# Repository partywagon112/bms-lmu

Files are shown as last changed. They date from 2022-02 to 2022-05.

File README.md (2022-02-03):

# Battery Management System - Local Measurement Unit

Final Year Research Project (FYRP) by Ethan Suter and Patrick Curtain to design a battery management system for an electric solar vehicle.

The Local Measurement Unit (LMU) is used to relay information about the cells to the Central Management Unit (CMU) that will they respond with balance target values for the LMU to act on. The LMU interconnects to the cell stack with the use of a terminal board, contained within the same repository. 

The LMU features an LTC6811 to monitor the cells, with two LTC3300 to actively balance the stack. These connect through multiple isolated SPI interfaces, to a microcontroller that is used to preprocess the data into a simpler form for the CMU to decypher.

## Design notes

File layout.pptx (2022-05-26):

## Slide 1

TEMP

TEMPERATURE

1

3

LV

OUT

10

IN

8

ABAL_1

5

PBAL

9

11

2

4

6

7

ABAL_2

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
RULES:
- The Active balancer, Passive balancer and temperature modules should be placed in proximity to the LV zone for SPI to cross isolation line
- 6 Must be adjacent to 7
- The balancer must be placed equidistance from each module in it’s balance group.
- The Temperature module should be placed on the ground that covers PBAL and ABAL (GND_LOWER)
- Along the vertical axis, each module should be in sequential order.

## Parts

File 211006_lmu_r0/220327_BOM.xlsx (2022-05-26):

Item | Qty | Reference(s) | Value | LibPart | Footprint | Datasheet | AVAILABILITY | Description | Height | MANUFACTURER | MAXIMUM_PACKAGE_HEIGHT | MP | Manufacturer | Mouser Part Number | Mouser Price/Stock | Mouser URL | PACKAGE | PARTREV | PRICE | Part Number | SNAPEDA_PACKAGE_ID | STANDARD | Voltage
1 | 1 | C1 | 220uF | Device:C_Polarized_US | Capacitor_SMD:CP_Elec_10x12.5 | ~ |  |  |  |  |  |  | Vishay | 594-MAL214699106E3 |  | https://au.mouser.com/ProductDetail/Vishay-BC-Components/MAL214699106E3 |  |  |  | MAL214699106E3
2 | 2 | C2, C3 | 10uF | Device:C | Capacitor_SMD:C_0805_2012Metric_Pad1.18x1.45mm_HandSolder | ~ |  |  |  |  |  |  |  |  |  |  |  |  |  | -
3 | 2 | C4, C6 | 22uF | Device:C | Capacitor_SMD:C_0805_2012Metric_Pad1.18x1.45mm_HandSolder | ~ |  |  |  |  |  |  |  |  |  |  |  |  |  | -
4 | 17 | C5, C12, C13, C25, C26, C27, C30, C103, C176, C177, C178, C179, C180, C181, C184, C185, C186 | 100nF | Device:C | Capacitor_SMD:C_0603_1608Metric_Pad1.08x0.95mm_HandSolder | ~ |  |  |  |  |  |  |  |  |  |  |  |  |  | -
5 | 22 | C7, C17, C18, C19, C20, C21, C22, C23, C24, C41, C53, C65, C77, C89, C101, C114, C126, C138, C150, C162, C174, C182 | 10nF | Device:C | Capacitor_SMD:C_0603_1608Metric_Pad1.08x0.95mm_HandSolder | ~ |  |  |  |  |  |  |  |  |  |  |  |  |  | -
6 | 4 | C8, C9, C10, C11 | DNP 10pF | Device:C | Capacitor_SMD:C_0603_1608Metric_Pad1.08x0.95mm_HandSolder | ~ |  |  |  |  |  |  |  |  |  |  |  |  |  | -
7 | 3 | C14, C15, C16 | 1uF | Device:C | Capacitor_SMD:C_0603_1608Metric_Pad1.08x0.95mm_HandSolder | ~ |  |  |  |  |  |  |  |  |  |  |  |  |  | -
8 | 2 | C28, C29 | 100nF | Device:C | Capacitor_SMD:C_0805_2012Metric_Pad1.18x1.45mm_HandSolder | ~ |  |  |  |  |  |  |  |  |  |  |  |  |  | -
9 | 72 | C31, C32, C34, C37, C39, C40, C43, C44, C46, C49, C51, C52, C55, C56, C58, C61, C63, C64, C67, C68, C70, C73, C75, C76, C79, C80, C82, C85, C87, C88, C91, C92, C94, C97, C99, C100, C104, C105, C107, C110, C112, C113, C116, C117, C119, C122, C124, C125, C128, C129, C131, C134, C136, C137, C140, C141, C143, C146, C148, C149, C152, C153, C155, C158, C160, C161, C164, C165, C167, C170, C172, C173 | 100uF | Device:C | Capacitor_SMD:C_1206_3216Metric_Pad1.33x1.80mm_HandSolder | ~ |  |  |  |  |  |  |  |  |  |  |  |  |  |  |  |  | 100V
10 | 12 | C33, C45, C57, C69, C81, C93, C106, C118, C130, C142, C154, C166 | 2.2nF | Device:C | Capacitor_SMD:C_0603_1608Metric_Pad1.08x0.95mm_HandSolder | ~ |  |  |  |  |  |  |  |  |  |  |  |  |  | -
11 | 36 | C35, C36, C38, C47, C48, C50, C59, C60, C62, C71, C72, C74, C83, C84, C86, C95, C96, C98, C108, C109, C111, C120, C121, C123, C132, C133, C135, C144, C145, C147, C156, C157, C159, C168, C169, C171 | 470pF | Device:C | Capacitor_SMD:C_0603_1608Metric_Pad1.08x0.95mm_HandSolder | ~ |  |  |  |  |  |  |  |  |  |  |  |  |  |  |  |  | 100V
12 | 12 | C42, C54, C66, C78, C90, C102, C115, C127, C139, C151, C163, C175 | DNP 10nF | Device:C | Capacitor_SMD:C_0805_2012Metric_Pad1.18x1.45mm_HandSolder | ~ |  |  |  |  |  |  |  |  |  |  |  |  |  |  |  |  | 100V
13 | 1 | C183 | 1uF | Device:C | Capacitor_SMD:C_0805_2012Metric_Pad1.18x1.45mm_HandSolder | ~ |  |  |  |  |  |  |  |  |  |  |  |  |  | -
14 | 1 | D1 | 1SMB5942B-13 | Device:D_TVS | Diode_SMD:D_SMB_Handsoldering | ~ |  |  |  |  |  |  | Diodes Inc | 621-1SMB5942B-13 |  | https://au.mouser.com/ProductDetail/Diodes-Incorporated/1SMB5942B-13?qs=uwKJARvjadMY8LI4ZfMqKA%3D%3D |  |  |  | 1SMB5942B-13
15 | 1 | D2 | SD560BTR | Device:D | Diode_SMD:D_SMB_Handsoldering | ~ |  |  |  |  |  |  | SMC Diode Solutions | NOT AVAILABLE! |  | NOT AVAILABLE! |  |  |  | SD560BTR
16 | 15 | D3, D4, D16, D18, D20, D22, D24, D26, D29, D31, D33, D35, D37, D39, D41 | LED (Red) | Device:LED | LED_SMD:LED_0805_2012Metric_Pad1.15x1.40mm_HandSolder | ~ |  |  |  |  |  |  | AMS OSRAM | 720-LSR976-NR-1 |  | https://au.mouser.com/ProductDetail/ams-OSRAM/LS-R976-NR-1-0-20-R18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 |  |  |  | LS R976-NR-1-0-20-R18
17 | 1 | D5 | NUP2105L | Power_Protection:NUP2105L | Package_TO_SOT_SMD:SOT-23 | http://www.onsemi.com/pub_link/Collateral/NUP2105L-D.PDF |  |  |  |  |  |  | ON Semiconductor | 863-SZNUP2105LT1G |  | https://au.mouser.com/ProductDetail/onsemi/SZNUP2105LT1G?qs=PJJcWtbOkNWqqZbXH80dfQ%3D%3D |  |  |  | NUP2105L
18 | 8 | D6, D7, D8, D9, D10, D11, D12, D13 | SMAZ5V6-13-F | Device:D_Zener | Diode_SMD:D_SMA_Handsoldering | ~ |  |  |  |  |  |  | Diodes Inc | NOT AVAILABLE! |  | NOT AVAILABLE! |  |  |  | SMAZ5V6-13-F
19 | 2 | D14, D27 | CMMSH2-40 | Device:D_Schottky | Diode_SMD:D_SOD-123F | ~ |  |  |  |  |  |  | Central Semiconductor | 610-CMMSH2-40TR |  | https://au.mouser.com/ProductDetail/Central-Semiconductor/CMMSH2-40-TR-PBFREE?qs=OlC7AqGiEDmeZ8mWO7SnhA%3D%3D |  |  |  | CMMSH2-40
20 | 12 | D15, D17, D19, D21, D23, D25, D28, D30, D32, D34, D36, D38 | SBR10U200P5-13 | SBR10U200P5-13:SBR10U200P5-13 | DIO_SBR10U200P5-13 |  |  |  |  | Diodes Inc |  |  | Diodes Inc | NOT AVAILABLE! |  | NOT AVAILABLE! |  |  |  | SBR10U200P5-13
21 | 2 | D40, D42 | LED (Blue) | Device:LED | LED_SMD:LED_0805_2012Metric_Pad1.15x1.40mm_HandSolder | ~ |  |  |  |  |  |  | Lumex | SML-LX0805USBC-TR |  | https://au.mouser.com/ProductDetail/Lumex/SML-LX0805USBC-TR?qs=jywnEC9mS4F%2FCvyk4BNITw%3D%3D |  |  |  | SML-LX0805USBC-TR
22 | 2 | D43, D44 | LED (Orange) | Device:LED | LED_SMD:LED_0805_2012Metric_Pad1.15x1.40mm_HandSolder | ~ |  |  |  |  |  |  | AMS OSRAM | 720-LOR976-PS-1 |  | https://au.mouser.com/ProductDetail/ams-OSRAM/LO-R976-PS-1-0-20-R18?qs=p6VZ%252BklCkRQY6bKwpfgF7g%3D%3D |  |  |  | LO R976-PS-1-0-20-R18
23 | 1 | F1 | Polyfuse 1A | Device:Polyfuse | Fuse:Fuse_2920_7451Metric_Castellated | ~ |  |  |  |  |  |  | Littelfuse | 530-0ZCF0100AF2A |  | https://au.mouser.com/ProductDetail/Bel-Fuse/0ZCF0100AF2A |  |  |  | 0ZCF0100AF2A
24 | 13 | F2, F3, F4, F5, F6, F7, F8, F9, F10, F11, F12, F13, F14 | Fuse | Device:Fuse | Fuse:Fuse_0805_2012Metric_Pad1.15x1.40mm_HandSolder | ~ |  |  |  |  |  |  | Vishay | 594-MFU0805FF04000P1 |  | https://au.mouser.com/ProductDetail/Vishay-Beyschlag/MFU0805FF04000P100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 |  |  |  | MFU0805FF04000P100
25 | 1 | FB1 | Ferrite Bead | Device:FerriteBead | Inductor_SMD:L_0603_1608Metric_Pad1.05x0.95mm_HandSolder | ~ |  |  |  |  |  |  | TDK | 810-MMZ0603S102HT000 |  | https://au.mouser.com/ProductDetail/TDK/MMZ0603S102HT000 |  |  |  | MMZ0603S102HT000
26 | 1 | IC1 | ADS7038QRTERQ1 | SamacSys_Parts:ADS7038QRTERQ1 | QFN50P300X300X80-17N-D | https://www.ti.com/lit/ds/symlink/ads7038-q1.pdf?ts=1609502413909 |  | ADS7038 Q1 Small 8 Channel 12 Bit ADC With SPI Interface and CRC | 0.8 |  |  |  | Texas Instruments | NOT AVAILABLE! | https://www.mouser.co.uk/ProductDetail/Texas-Instruments/ADS7038QRTERQ1?qs=81r%252BiQLm7BTk46c4kXEtDw%3D%3D | NOT AVAILABLE! |  |  |  | ADS7038QRTERQ1
27 | 2 | J1, J2 | Conn_02x03_Odd_Even | Connector_Generic:Conn_02x03_Odd_Even | Connector_Molex:Molex_Mini-Fit_Jr_5566-06A_2x03_P4.20mm_Vertical | ~ |  |  |  |  |  |  |  |  |  |  |  |  |  | -
28 | 1 | J3 | Conn_02x08_Odd_Even | Connector_Generic:Conn_02x08_Odd_Even |  | ~ |  |  |  |  |  |  |  |  |  |  |  |  |  | -
29 | 1 | J4 | Conn_01x13 | Connector_Generic:Conn_01x13 |  | ~ |  |  |  |  |  |  |  |  |  |  |  |  |  | -
30 | 3 | J5, J6, J12 | Conn_01x03 | Connector_Generic:Conn_01x03 | Connector_PinHeader_2.54mm:PinHeader_1x03_P2.54mm_Vertical | ~ |  |  |  |  |  |  |  |  |  |  |  |  |  | -
31 | 4 | J7, J8, J9, J10 | Conn_01x02 | Connector_Generic:Conn_01x02 | Connector_PinHeader_2.54mm:PinHeader_1x02_P2.54mm_Vertical | ~ |  |  |  |  |  |  |  |  |  |  |  |  |  | -
32 | 1 | J11 | Conn_ARM_JTAG_SWD_10 | Connector:Conn_ARM_JTAG_SWD_10 | Connector_PinHeader_1.27mm:PinHeader_2x09_P1.27mm_Vertical_SMD | http://infocenter.arm.com/help/topic/com.arm.doc.ddi0314h/DDI0314H_coresight_components_trm.pdf
33 | 1 | K1 | G5V-2 | Relay:G5V-2 | Relay_THT:Relay_DPDT_Omron_G5V-2 | http://omronfs.omron.com/en_US/ecb/products/pdf/en-g5v_2.pdf |  |  |  |  |  |  | Omron | 653-G5V-2-H1-DC12 |  | https://au.mouser.com/ProductDetail/Omron-Electronics/G5V-2-H1-DC12?qs=SXIVkn%252Bm38kUovfCr9o1Dw%3D%3D |  |  |  | G5V-2-H1-DC12
34 | 1 | L1 | 744272121 | Device:L_Ferrite_Coupled | Inductor_SMD:L_CommonModeChoke_Wuerth_WE-SL5 | ~ |  |  |  |  |  |  | Wurth | 710-744272121 |  | https://au.mouser.com/ProductDetail/Wurth-Elektronik/744272121?qs=PGXP4M47uW7bXHmb3ZYlsQ%3D%3D |  |  |  | 744272121
35 | 1 | L2 | 0ZCF0100AF2A | Device:L_Ferrite_Coupled | Inductor_SMD:L_CommonModeChoke_Coilcraft_1812CAN | ~ |  |  |  |  |  |  | EPCOS - TDK | 871-B82787C104H2 |  | https://au.mouser.com/ProductDetail/EPCOS-TDK/B82787C0104H002?qs=C9xViIFka8ni2PxKXbJHjQ%3D%3D |  |  |  | B82787C0104H002
36 | 1 | PS1 | R2S-053.3 | R2S-053.3:R2S-053.3 | CONV_R2S-053.3 |  |  |  |  | RECOM | 9.0mm |  | RECOM | 919-R2S-053.3 |  | https://au.mouser.com/ProductDetail/RECOM-Power/R2S-0533?qs=XF8hdbuHJAU8%2FoDdSFUU9w%3D%3D |  | 0 |  | 919-R2S-053.3 |  | Manufacturer Recommendations
37 | 1 | Q1 | CZT5551 | czt5551:CZT5551 | Package_TO_SOT_SMD:SOT-223-3_TabPin2 | https://www.onsemi.com/pub/Collateral/PN2222-D.PDF |  |  |  |  |  |  | Central Semiconductor | 610-CZT5551 |  | https://au.mouser.com/ProductDetail/Central-Semiconductor/CZT5551-TR-PBFREE?qs=u16ybLDytRb99SsaOAvs%2FQ%3D%3D |  |  |  | CZT5551
38 | 12 | Q2, Q5, Q8, Q11, Q14, Q17, Q20, Q23, Q26, Q29, Q32, Q35 | BSS308PE | bss308pe_2:BSS308PE | Package_TO_SOT_SMD:SOT-23 | https://www.infineon.com/dgdl/BSS308PE_Rev2.03.pdf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 |  |  |  |  |  |  | Infineon Technologies | 726-BSS308PEH6327SA1 |  | https://au.mouser.com/ProductDetail/Infineon-Technologies/BSS308PEH6327XT?qs=qsgX%252BAP2E5D1TWlnsTlotQ%3D%3D |  |  |  | BSS308PEH6327XT
39 | 24 | Q3, Q4, Q6, Q7, Q9, Q10, Q12, Q13, Q15, Q16, Q18, Q19, Q21, Q22, Q24, Q25, Q27, Q28, Q30, Q31, Q33, Q34, Q36, Q37 | SiR882DP | sir882dp:SiR882DP | Package_SO:PowerPAK_SO-8_Single | https://www.vishay.com/docs/73152/si7336adp.pdf |  |  |  |  |  |  | Vishay | 78-SIR882DP-T1-GE3 |  | https://au.mouser.com/ProductDetail/Vishay-Semiconductors/SIR882DP-T1-GE3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 |  |  |  | SIR882DP-T1-GE3
40 | 1 | Q38 | BC817 | Transistor_BJT:BC817 | Package_TO_SOT_SMD:SOT-23 | https://www.onsemi.com/pub/Collateral/BC818-D.pdf |  |  |  |  |  |  | Nexperia | 771-BC817-40-T/R |  | https://au.mouser.com/ProductDetail/Nexperia/BC817-40215 |  |  |  | BC817
41 | 7 | R1, R2, R242, R243, R244, R245, R246 | 2.2kR | Device:R | Resistor_SMD:R_0603_1608Metric_Pad0.98x0.95mm_HandSolder | ~ |  |  |  |  |  |  |  |  |  |  |  |  |  | -
42 | 2 | R3, R4 | 60R | Device:R | Resistor_SMD:R_0805_2012Metric_Pad1.20x1.40mm_HandSolder | ~ |  |  |  |  |  |  |  |  |  |  |  |  |  | -
43 | 1 | R5 | 0R | Device:R | Resistor_SMD:R_0805_2012Metric_Pad1.20x1.40mm_HandSolder | ~ |  |  |  |  |  |  |  |  |  |  |  |  |  | -
44 | 9 | R6, R8, R10, R12, R14, R16, R18, R20, R204 | 10kR | Device:R | Resistor_SMD:R_0603_1608Metric_Pad0.98x0.95mm_HandSolder | ~ |  |  |  |  |  |  |  |  |  |  |  |  |  | -
45 | 55 | R7, R9, R11, R13, R15, R17, R19, R21, R111, R112, R113, R114, R115, R116, R117, R118, R203, R205, R206, R207, R208, R209, R210, R211, R212, R213, R214, R215, R216, R217, R218, R219, R220, R221, R222, R223, R224, R225, R226, R227, R228, R229, R230, R231, R232, R233, R234, R235, R236, R237, R238, R239, R240, R241, R247 | 50kR | Device:R | Resistor_SMD:R_0603_1608Metric_Pad0.98x0.95mm_HandSolder | ~ |  |  |  |  |  |  |  |  |  |  |  |  |  | -
46 | 3 | R22, R28, R128 | 1MR | Device:R | Resistor_SMD:R_0603_1608Metric_Pad0.98x0.95mm_HandSolder | ~ |  |  |  |  |  |  |  |  |  |  |  |  |  | -
47 | 2 | R23, R24 | DNP | Device:R | Resistor_SMD:R_0805_2012Metric_Pad1.20x1.40mm_HandSolder | ~ |  |  |  |  |  |  |  |  |  |  |  |  |  | -
48 | 2 | R25, R26 | 100R | Device:R | Resistor_SMD:R_1206_3216Metric_Pad1.30x1.75mm_HandSolder | ~ |  |  |  |  |  |  |  |  |  |  |  |  |  | -
49 | 2 | R27, R127 | 6.81R | Device:R | Resistor_SMD:R_0603_1608Metric_Pad0.98x0.95mm_HandSolder | ~ |  |  |  |  |  |  |  |  |  |  |  |  |  | -
50 | 2 | R29, R129 | 23.7kR | Device:R | Resistor_SMD:R_0603_1608Metric_Pad0.98x0.95mm_HandSolder | ~ |  |  |  |  |  |  |  |  |  |  |  |  |  | -
51 | 2 | R30, R130 | 33.2kR | Device:R | Resistor_SMD:R_0603_1608Metric_Pad0.98x0.95mm_HandSolder | ~ |  |  |  |  |  |  |  |  |  |  |  |  |  | -
52 | 12 | R31, R43, R55, R67, R79, R91, R131, R143, R155, R167, R179, R191 | 330R | Device:R | Resistor_SMD:R_1206_3216Metric_Pad1.30x1.75mm_HandSolder | ~ |  |  |  |  |  |  |  |  |  |  |  |  |  | -
53 | 12 | R32, R44, R56, R68, R80, R92, R132, R144, R156, R168, R180, R192 | 470R | Device:R | Resistor_SMD:R_0603_1608Metric_Pad0.98x0.95mm_HandSolder | ~ |  |  |  |  |  |  |  |  |  |  |  |  |  | -
54 | 12 | R33, R45, R57, R69, R81, R93, R133, R145, R157, R169, R181, R193 | 3.3kR | Device:R | Resistor_SMD:R_0603_1608Metric_Pad0.98x0.95mm_HandSolder | ~ |  |  |  |  |  |  |  |  |  |  |  |  |  | -
55 | 24 | R34, R41, R46, R53, R58, R65, R70, R77, R82, R89, R94, R101, R134, R141, R146, R153, R158, R165, R170, R177, R182, R189, R194, R201 | 5.1R | Device:R | Resistor_SMD:R_0603_1608Metric_Pad0.98x0.95mm_HandSolder | ~ |  |  |  |  |  |  |  |  |  |  |  |  |  | -
56 | 24 | R35, R40, R47, R52, R59, R64, R71, R76, R83, R88, R95, R100, R135, R140, R147, R152, R159, R164, R171, R176, R183, R188, R195, R200 | 20R | Device:R | Resistor_SMD:R_0603_1608Metric_Pad0.98x0.95mm_HandSolder | ~ |  |  |  |  |  |  |  |  |  |  |  |  |  | -
57 | 24 | R36, R38, R48, R50, R60, R62, R72, R74, R84, R86, R96, R98, R136, R138, R148, R150, R160, R162, R172, R174, R184, R186, R196, R198 | 20R | Device:R | Resistor_SMD:R_1206_3216Metric_Pad1.30x1.75mm_HandSolder | ~ |  |  |  |  |  |  |  |  |  |  |  |  |  | -
58 | 24 | R37, R39, R49, R51, R61, R63, R73, R75, R85, R87, R97, R99, R137, R139, R149, R151, R161, R163, R173, R175, R185, R187, R197, R199 | 25mR | Device:R | Resistor_SMD:R_1206_3216Metric_Pad1.30x1.75mm_HandSolder | ~
59 | 12 | R42, R54, R66, R78, R90, R102, R142, R154, R166, R178, R190, R202 | 100R | Device:R | Resistor_SMD:R_0603_1608Metric_Pad0.98x0.95mm_HandSolder | ~ |  |  |  |  |  |  |  |  |  |  |  |  |  | -
60 | 16 | R103, R104, R105, R106, R107, R108, R109, R110, R119, R120, R121, R122, R123, R124, R125, R126 | DNP 50k | Device:R | Resistor_SMD:R_0603_1608Metric_Pad0.98x0.95mm_HandSolder | ~ |  |  |  |  |  |  |  |  |  |  |  |  |  | -
61 | 1 | SW1 | SW_Push | Switch:SW_Push | Button_Switch_SMD:SW_SPST_Omron_B3FS-100xP | ~
62 | 1 | SW2 | SW_SPST | Switch:SW_SPST | Button_Switch_SMD:SW_DIP_SPSTx01_Slide_9.78x4.72mm_W8.61mm_P2.54mm | ~
63 | 12 | T1, T2, T3, T4, T5, T6, T7, T8, T9, T10, T11, T12 | 750312504 | 750312504:750312504 | EP13_SMT_H_8PIN_(750312504) |  |  |  |  |  |  |  | Wurth | NOT AVAILABLE! |  | NOT AVAILABLE! |  |  |  | 750312504
64 | 160 | TP1, TP2, TP3, TP4, TP5, TP6, TP7, TP8, TP9, TP10, TP11, TP12, TP13, TP14, TP15, TP16, TP17, TP18, TP19, TP20, TP21, TP22, TP23, TP24, TP25, TP26, TP27, TP28, TP29, TP30, TP31, TP32, TP33, TP34, TP35, TP36, TP37, TP38, TP39, TP40, TP41, TP42, TP43, TP44, TP45, TP46, TP47, TP48, TP49, TP50, TP51, TP52, TP53, TP54, TP55, TP56, TP57, TP58, TP59, TP60, TP61, TP62, TP63, TP64, TP65, TP66, TP67, TP68, TP69, TP70, TP71, TP72, TP73, TP74, TP75, TP76, TP77, TP78, TP79, TP80, TP81, TP82, TP83, TP84, TP85, TP86, TP87, TP88, TP89, TP90, TP91, TP92, TP93, TP94, TP95, TP96, TP97, TP98, TP99, TP100, TP101, TP102, TP103, TP104, TP105, TP106, TP107, TP108, TP109, TP110, TP111, TP112, TP113, TP114, TP115, TP116, TP117, TP118, TP119, TP120, TP121, TP122, TP123, TP124, TP125, TP126, TP127, TP128, TP129, TP130, TP131, TP132, TP133, TP134, TP135, TP136, TP137, TP138, TP139, TP140, TP141, TP142, TP143, TP144, TP145, TP146, TP147, TP148, TP149, TP150, TP151, TP152, TP153, TP154, TP155, TP156, TP157, TP158, TP159, TP160 | TestPoint | Connector:TestPoint | TestPoint:TestPoint_Pad_D1.0mm | ~ |  |  |  |  |  |  | - | - |  | - |  |  |  | -
65 | 1 | U1 | R-78C5.0-1.0 | Regulator_Switching:R-78C5.0-1.0 | Converter_DCDC:Converter_DCDC_RECOM_R-78E-0.5_THT | https://www.recom-power.com/pdf/Innoline/R-78Cxx-1.0.pdf |  |  |  |  |  |  | RECOM | 919-R-78C5.0-1.0 |  | https://au.mouser.com/ProductDetail/RECOM-Power/R-78C50-10?qs=sGAEpiMZZMs7Ab1RACNF3AuU4LGLjBGD4EiimKouwhs%3D |  |  |  | R-78C5.0-1.0
66 | 1 | U2 | ISO1042DWVR | ISO1042DWVR:ISO1042DWVR | SOIC127P1150X280-8N |  |  |  |  |  |  |  | Texas Instruments | NOT AVAILABLE! |  | NOT AVAILABLE! |  |  |  | ISO1042DWVR
67 | 1 | U3 | LTC6811HG-2#PBF | LTC6811HG-2_PBF:LTC6811HG-2#PBF | SOP50P780X200-48N |  |  |  |  | Linear Technology |  |  | Linear Technology | NOT AVAILABLE! |  | NOT AVAILABLE! |  |  |  | LTC6811HG-2#PBF
68 | 2 | U4, U5 | LTC3300ILXE-2#PBF | LTC3300ILXE-2_PBF:LTC3300ILXE-2#PBF | QFP50P900X900X160-49N |  | Unavailable |  |  | Linear Technology |  | LTC3300ILXE-2#PBF | Linear Technology | NOT AVAILABLE! |  | NOT AVAILABLE! | LQFP-48 Linear Technology | A | 10.07 USD | LTC3300ILXE-2#PBF | 29275 | IPC-7351B
69 | 3 | U6, U7, U8 | ISO7761DBQ | Isolator:ISO7761DBQ | Package_SO:SSOP-16_3.9x4.9mm_P0.635mm | https://www.ti.com/lit/ds/symlink/iso7763.pdf |  |  |  |  |  |  | Texas Instruments | NOT AVAILABLE! |  | NOT AVAILABLE! |  |  |  | ISO7761DBQ
70 | 1 | U9 | STM32F103C8Tx | MCU_ST_STM32F1:STM32F103C8Tx | Package_QFP:LQFP-48_7x7mm_P0.5mm | http://www.st.com/st-web-ui/static/active/en/resource/technical/document/datasheet/CD00161566.pdf |  |  |  |  |  |  | ST Microelectronics | NOT AVAILABLE! |  | NOT AVAILABLE! |  |  |  | STM32F103C8Tx
71 | 1 | Y1 | 16MHz | Device:Crystal_GND23 | Crystal:Crystal_SMD_3225-4Pin_3.2x2.5mm_HandSoldering | ~ |  |  |  |  |  |  | ABRACON | 815-M8AIG-16-12-2ZT3 |  | https://au.mouser.com/ProductDetail/ABRACON/ABM8AIG-16000MHZ-12-2Z-T3?qs=gG6m684uYP7glnqUpaQmDA%3D%3D |  |  |  | ABM8AIG-16.000MHZ-12-2Z-T3

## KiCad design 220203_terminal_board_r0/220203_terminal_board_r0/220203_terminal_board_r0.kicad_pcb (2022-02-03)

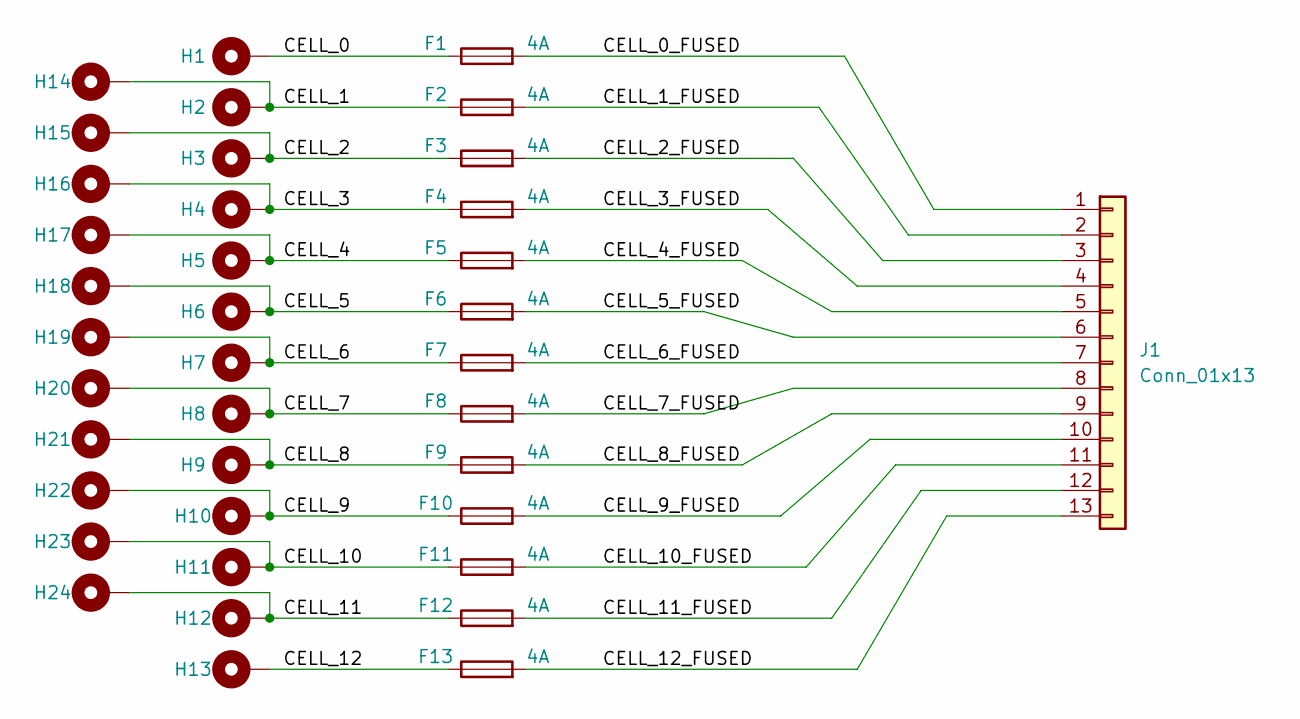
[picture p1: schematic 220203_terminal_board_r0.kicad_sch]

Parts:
F1, F2, F3, F4, F5, F6, F7, F8, F9, F10, F11, F12, F13: 4A; Fuse_0805_2012Metric_Pad1.15x1.40mm_HandSolder
H1, H2, H3, H4, H5, H6, H7, H8, H9, H10, H11, H12, H13, H14, H15, H16, H17, H18, H19, H20, H21, H22, H23, H24: MountingHole_Pad; MountingHole_4.3mm_M4_Pad_Via
J1: Conn_01x13

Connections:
/CELL_0: F1.1, H1.1
/CELL_0_FUSED: F1.2, J1.1
/CELL_1: F2.1, H2.1, H14.1
/CELL_1_FUSED: F2.2, J1.2
/CELL_2: F3.1, H3.1, H15.1
/CELL_2_FUSED: F3.2, J1.3
/CELL_3: F4.1, H4.1, H16.1
/CELL_3_FUSED: F4.2, J1.4
/CELL_4: F5.1, H5.1, H17.1
/CELL_4_FUSED: F5.2, J1.5
/CELL_5: F6.1, H6.1, H18.1
/CELL_5_FUSED: F6.2, J1.6
/CELL_6: F7.1, H7.1, H19.1
/CELL_6_FUSED: F7.2, J1.7
/CELL_7: F8.1, H8.1, H20.1
/CELL_7_FUSED: F8.2, J1.8
/CELL_8: F9.1, H9.1, H21.1
/CELL_8_FUSED: F9.2, J1.9
/CELL_9: F10.1, H10.1, H22.1
/CELL_9_FUSED: F10.2, J1.10
/CELL_10: F11.1, H11.1, H23.1
/CELL_10_FUSED: F11.2, J1.11
/CELL_11: F12.1, H12.1, H24.1
/CELL_11_FUSED: F12.2, J1.12
/CELL_12: F13.1, H13.1
/CELL_12_FUSED: F13.2, J1.13

Board: 2 copper layers, 37 parts (0 on the bottom side), 13 nets, no tracks yet.

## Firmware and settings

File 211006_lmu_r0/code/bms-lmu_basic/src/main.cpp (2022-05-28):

#include <Arduino.h>
#include "bms_lmu.h"
#include "SPI.h"
#include <eXoCAN.h>
#include "TickerInterrupt.h"

/******************************************************************************
 * BMS_LMU - HARDWARE REVISION 0
 * Patrick Curtain
 * 
 * Battery Management System - Local Measurement Unit
 * 
 * An active balancer created for FYRP by Patrick Curtain and Ethan Suter, 
 * Semester 2 2021 and Semester 1 2022, at Swinburne University of Technology.
 * 
 * Code base derived from Team Swinburne FSAE
 * Available: https://github.com/Team-Swinburne/ts_20-code-development
 * 
 * Revision     Date      Comments
 * --------   --------    --------
 * 0.0        28/5/2022   Initial Code Base
 * 
 * 
******************************************************************************/

// PINOUT
#define LED0 PC13
#define CAN_TX_LED PB5
#define CAN_RX_LED PB6
#define SPI_TX_LED PB7
#define SPI_RX_LED PB8
#define FAULT_RELAY PA9
#define FAULT_RELAY_FEEDBACK PA10

// NOT SAFETY PARAMETERS
#define DISCHARGE_TIMER_LIMIT 1000
#define HEART_RATE 1000
#define CAN_INTERVAL 800
#define CANBUS_FREQUENCY 250000

#define TX_ADDRESS 0x481

// led pins
DigitalOut can_tx_led(CAN_TX_LED);
DigitalOut can_rx_led(CAN_TX_LED);
DigitalOut spi_tx_led(CAN_TX_LED);
DigitalOut spi_rx_led(CAN_TX_LED);

// Globals
Heartbeat heartbeat(FAULT_RELAY, FAULT_RELAY_FEEDBACK, LED0);
Stack stack;
PBalancer passive_balancer(stack, DISCHARGE_TIMER_LIMIT);

// Interfaces
eXoCAN can;

// Timers
TickerInterrupt ticker(TIM2, 1);

struct msg_frame
{
  uint8_t len = 8;
  uint8_t bytes[8] = {0};
};

static msg_frame	heart_frame {.len = 3},
               	bms_lower_bank {.len = 6}, 
				        bms_upper_bank {.len = 6},
               	temperature {.len = 8};

uint8_t rxData[8];

void can_tx(){
  can.transmit(TX_ADDRESS, heart_frame.bytes, heart_frame.len);
  can.transmit(TX_ADDRESS + 1, bms_lower_bank.bytes, bms_lower_bank.len);
  can.transmit(TX_ADDRESS + 2, bms_upper_bank.bytes, bms_upper_bank.len);
  can.transmit(TX_ADDRESS + 3, temperature.bytes, temperature.len);

  can_tx_led = !can_tx_led;
}

// Can receive interupt service routine
void canISR() {
	can.rxMsgLen = can.receive(can.id, can.fltIdx, can.rxData.bytes);
}


void can_rx() {
	if (can.rxMsgLen > -1) {
    can_rx_led = !can_rx_led;
	}
}

uint8_t array_to_uint8(bool arr[], int count){
    int ret = 0;
    int tmp;
    for (int i = 0; i < count; i++) {
        tmp = arr[i];
        ret |= tmp << (count - i - 1);
    }
    return ret;
}

uint16_t check_errors(){
  bool error_code[8];

	error_code[ERROR_OV_FAULT] = stack.ov_fault();
	error_code[ERROR_UV_FAULT] = stack.uv_fault();
	// error_code[ERROR_OT_FAULT] = !imd.get_IMD_ok();
	error_code[ERROR_RELAY_FAULT] = heartbeat.relay_fault();
	
	// error_code[ERROR_ORION_LOW_VOTLAGE] 	= orion.check_low_voltage();
	// error_code[ERROR_ORION_HIGH_VOLTAGE] 	= orion.check_high_voltage();
	// error_code[ERROR_ORION_OVERTEMPERATURE] = orion.check_overtemperature();
	// error_code[ERROR_PERIPHERALS] = 0;

	return array_to_uint8(error_code, 8);
}

void update_can_frames(){
  heart_frame.bytes[0] = heartbeat.state();
  heart_frame.bytes[0] = heartbeat.counter();
  heart_frame.bytes[1] = heartbeat.fault_code();

  for (int i = 0; i < 6; i++){
    bms_lower_bank.bytes[i] = stack.cell_voltage(i);
  }

  for (int i = 6; i < 12; i++){
    bms_upper_bank.bytes[i] = stack.cell_voltage(i);
  }

  // add in the temp measurement thing.
}

void state_d(){

  update_can_frames();

  switch(heartbeat.state()) {
    case (FAULT):
      // do nothing, clear the error as quickly
      // as possible.
      if (check_errors() == 0){
        heartbeat.state(IDLE);
      }
      break;
    
    case (IDLE):
      // literally do nothing!
      break;
    
    case (MEASURING):
      // stop balancing
      passive_balancer.end_balance();

      // check the passive balancer
      passive_balancer.update_stack();

      // measure the temperatures
      break;
    
    case (PASSIVE_BALANCING):
      passive_balancer.start_balance();
      break;
    
    case (ACTIVE_BALANCING):
      // not sure yet!
      break;
  }
}

void start_up_lights(){
  pinMode(PB5, OUTPUT);
  pinMode(PB6, OUTPUT);
  pinMode(PB7, OUTPUT);
  pinMode(PB8, OUTPUT);

  int scroller_time = 100;
  digitalWrite(PB5, HIGH);
  delay(scroller_time);
  digitalWrite(PB6, HIGH);
  delay(scroller_time);
  digitalWrite(PB7, HIGH);
  delay(scroller_time);
  digitalWrite(PB8, HIGH);
  delay(scroller_time);

  digitalWrite(PB5, LOW);
  delay(scroller_time);
  digitalWrite(PB6, LOW);
  delay(scroller_time);
  digitalWrite(PB7, LOW);
  delay(scroller_time);
  digitalWrite(PB8, LOW);
  delay(scroller_time);
}


// timer functions
void heartbeat_cb(){
  heartbeat.tick(check_errors());
}

void setup() {

  // start the heartbeat timer.
  start_up_lights();

  // setup the can
  can.begin(STD_ID_LEN, CANBUS_FREQUENCY, PORTA_11_12_WIRE_PULLUP);   //11 Bit Id, 500Kbps
  can.filterMask16Init(0, 0x600, 0x7ff);
  can.attachInterrupt(canISR);
  
  // setup heartbeat tickers.
  ticker.start();
  ticker.attach(heartbeat_cb, HEART_RATE);

  ticker.attach(can_tx, CAN_INTERVAL);
}

void loop() {
  // state_d();

  delay(1000);
}

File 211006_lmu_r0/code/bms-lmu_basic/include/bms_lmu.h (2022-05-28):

#include <Arduino.h>

#define STACK_SIZE 12

// SAFETY PARAMETERS!
#define MAX_VOLTAGE 4.2
#define MIN_VOLTAGE 2.8
#define MAX_TEMPERATURE 60

// State Machine Logic
enum LMU_States {
  FAULT, 
  IDLE, 
  MEASURING,
  PASSIVE_BALANCING, 
  ACTIVE_BALANCING
} lmu_state_t;

typedef enum ERROR_CODES_SUB_KEY{
    ERROR_OV_FAULT,
    ERROR_UV_FAULT,
    ERROR_OT_FAULT,
    ERROR_RELAY_FAULT
} error_state_t;

class DigitalOut {
  private:
    uint32_t _pin_number;

  public:
    DigitalOut(uint32_t pin_number){
      _pin_number = pin_number;
      pinMode(_pin_number, OUTPUT);
    }

    int read(){
      return digitalRead(_pin_number);
    }

    void write(uint32_t state){
      digitalWrite(_pin_number, state);
    }

    DigitalOut &operator= (uint32_t value){
      digitalWrite(_pin_number, value);
      return *this;
    }

    DigitalOut &operator= (DigitalOut &rhs);

    operator int() {
      return read();
    }
};

class DigitalIn {
    private:
        uint32_t _pin_number;

    public:
        DigitalIn(uint32_t pin_number){
            _pin_number = pin_number;
            pinMode(_pin_number, INPUT);
        }

        int read() {
            return digitalRead(_pin_number);
        }

        operator int(){
            return read();
        }
};

class Heartbeat {
  private:
    DigitalOut fault_relay;
    DigitalOut heartbeat_led;

    DigitalIn fault_relay_feedback;

    int _counter;
    LMU_States _state;
    uint8_t _fault_code;

  public:
    Heartbeat(uint32_t fault_relay_pin, uint32_t fault_relay_feedback_pin, uint32_t heartbeat_led_pin) : 
    fault_relay(fault_relay_pin), fault_relay_feedback(fault_relay_feedback_pin), heartbeat_led(heartbeat_led_pin) {
      _counter = 0;
      _state = FAULT;
    }

    // increments counter if healthy. must be associated with a timer of some sort.
    void tick(uint8_t fault_code){
        _fault_code = fault_code;
      if (fault_code == 0){
        _counter = _counter + 1;
        fault_relay = 1;
        heartbeat_led = !heartbeat_led;
      } else {
        _counter = 0;
        fault_relay = 0;
      }
    }

    int counter(){
      return _counter;
    }

    LMU_States state(){
      return _state;
    }

    void state(LMU_States new_state){
      _state = new_state;
    }

    bool relay_fault(){
        return fault_relay != fault_relay_feedback;
    }

    uint8_t fault_code(){
        return _fault_code;
    }
};

class Stack {
  private: 
    uint16_t cells[STACK_SIZE];

  public:
    uint16_t cell_voltage(int cell_number){
        return cells[cell_number];
    }

    bool update_cell(int pos, uint16_t cell_voltage){
      if (pos >= STACK_SIZE || pos < 0) {
        return false;
      } else {
        cells[pos] = cell_voltage;
        return true;
      }
    }

    uint16_t min(){
      uint16_t lowest_cell = cells[0];
      for (int i = 0; i < STACK_SIZE; i++){
        if (lowest_cell > cells[i]) {
          lowest_cell = cells[i];
        }
      }
      return lowest_cell;
    }

    uint16_t max(){
      uint16_t highest_cell = cells[0];
      for (int i = 0; i < STACK_SIZE; i++){
        if (highest_cell < cells[i]) {
          highest_cell = cells[i];
        }
      }
      return highest_cell;
    }

    float average(){
      return (float)sum_stack_voltage()/STACK_SIZE;
    }

    int sum_stack_voltage(){
      int sum = 0;
      for (int i = 0; i < STACK_SIZE; i++){
        sum = sum + cells[i];
      }
      return sum;
    }

    bool ov_fault(){
        return (max() > MAX_VOLTAGE);
    }

    bool uv_fault(){
        return (min() < MIN_VOLTAGE);
    }
};

class PBalancer {
  private:
    Stack _stack;

  public:
    PBalancer(){

    }

    PBalancer(Stack &stack, uint16_t dtl){

    }

    void start_balance(){

    }

    void end_balance(){

    }

    void update_stack(){

    }

    bool pbalance_ok(){

    }
};

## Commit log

2021-10-10 Added new a-balancer interface
    [211006_lmu_r0.sch, active_passive_balance.sch, file615D6D62.sch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]
2021-11-01 LMU design init
    [211006_lmu_r0.sch, active_passive_balance.sch, file615D6D62.sch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]
2022-01-27 Finished schematic, ready for pcb layout
    [211006_lmu_r0.sch, Address Selection.sch, Lower Active Balance Group.sch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]
2022-01-27 Changed some directories
    [211006_lmu_r0.kicad_pcb, 211006_lmu_r0.sch, Address Selection.sch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]
2022-01-27 inverted logic for the LMS fault detection relay
    [active_passive_balance.sch, file615D6DD2.sch, file61619F33.sch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]
2022-01-28 Updated BOM and footprints for non-hv components
    [211006_lmu_r0.sch, Address Selection.sch, Lower Active Balance Group.sch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]
2022-01-28 Added most footprint requirements in HV
    [211006_lmu_r0.sch, Lower Active Balance Group.sch, Lower Address Selection.sch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]
2022-01-28 Cleaned up last components missing footprint refs
    [211006_lmu_r0.sch, Address Selection.sch, Lower Active Balance Group.sch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]
2022-01-30 Updated with Mouser links for BOM
    [211006_lmu_r0.sch, Address Selection.sch, Lower Active Balance Group.sch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]
2022-02-03 added terminal board
    [220203_terminal_board_r0.kicad_pcb, 220203_terminal_board_r0.kicad_sch]
2022-02-03 changed to M4 terminal boards
    [220203_terminal_board_r0.kicad_sch]
2022-02-03 minor BOM changes
    [220203_terminal_board_r0.kicad_pcb, file6196A5FB.sch]
2022-02-05 Updated lmu project files to Kicad V6
    Using V6.0.1
    [211006_lmu_r0.kicad_pcb, 211006_lmu_r0.kicad_sch, Address Selection.kicad_sch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]
2022-02-05 Updated lmu project with relative library paths and fixed broken symbols
    [211006_lmu_r0.kicad_sch, Address Selection.kicad_sch, Lower Address Selection.kicad_sch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]
2022-02-05 Updated lmu footprint lib paths, fixed most footprint errors
2022-02-16 Began LMU pcb layout
    [211006_lmu_r0.kicad_pcb]
2022-03-16 Close to completing front side of 4-module board
    [211006_lmu_r0.kicad_pcb]
2022-03-20 Installed and tested Replicate Layout plugin
    Next to do: Finalise design of singular balancing module and then start layout of large board.
    Things to update:
    - Change orientation of FETs underneath coil, add vias and copper pour on opposite side for heat dissipation
    - standardise all via stitching of all large traces to grid of small vias
    - Route last few traces
    - Ensure all traces coming of bottom side of "module" - will help with routing all traces once modules are replicated
    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
    [211006_lmu_r0.kicad_pcb]
2022-03-25 Balance module design finalised
    [211006_lmu_r0.kicad_pcb]
2022-03-25 Fixed missed component in module
    [211006_lmu_r0.kicad_pcb]
2022-03-25 Module replication successful
    [211006_lmu_r0.kicad_pcb]
2022-03-27 Updated some components to make sourcing easier
    [211006_lmu_r0.kicad_sch, 220327_BOM.xlsx, Address Selection.kicad_sch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]
2022-03-27 Continued layout of board sections
    [211006_lmu_r0.kicad_pcb, file6196A5FB.kicad_sch, temperature_sensor_input_filter.kicad_sch]
2022-03-29 fixed footprints for headers, started planning out zones
    [211006_lmu_r0.kicad_pcb, 211006_lmu_r0.kicad_sch, Upper Address Selection.kicad_sch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]
2022-03-30 Lots of routing and placing, according to planned layout
    [211006_lmu_r0.kicad_pcb, 211006_lmu_r0.kicad_sch, Upper Address Selection.kicad_sch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]
2022-04-05 Finishing up the power supply, starting the CAN transceiver group
    [211006_lmu_r0.kicad_pcb]
2022-04-05 Fixed stuff
    [211006_lmu_r0.kicad_pcb]
2022-04-06 CAN transceiver stuff almost done, still needs CAN_S finished
    [211006_lmu_r0.kicad_pcb, 211006_lmu_r0.kicad_sch, temperature_sensor_input_filter.kicad_sch]
2022-04-13 CAN_S Finished, refining balancer module
    [211006_lmu_r0.kicad_pcb]
2022-04-19 added gantt chart
    [gantt_chart.xlsx]
2022-04-19 progress on PCB
    [211006_lmu_r0.kicad_pcb]
2022-04-19 final merge before branch
    [211006_lmu_r0.kicad_sch, active_passive_balance.kicad_sch, file6196A5FB.kicad_sch]
2022-04-20 updated pcb still need to find j11
    [211006_lmu_r0.kicad_pcb, 211006_lmu_r0.kicad_sch, active_passive_balance.kicad_sch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]
2022-04-20 fixed issues on higher cells, study into how to route
    [211006_lmu_r0.kicad_pcb, active_passive_balance.kicad_sch, file616BA637.kicad_sch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]
2022-04-20 refined in-out routing mechanism
    [211006_lmu_r0.kicad_pcb, 211006_lmu_r0.kicad_sch, active_passive_balance.kicad_sch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]
2022-04-20 started layout
    [211006_lmu_r0.kicad_pcb, 211006_lmu_r0.kicad_sch, file615D6D62.kicad_sch]
2022-04-20 unique traces for each tap, going towards front
    [211006_lmu_r0.kicad_pcb]
2022-04-20 quick save
    [211006_lmu_r0.kicad_pcb]
2022-04-20 little bit closer
    [211006_lmu_r0.kicad_pcb, 211006_lmu_r0.kicad_sch, active_passive_balance.kicad_sch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]
2022-04-21 updated gantt chart
    [gantt_chart.xlsx]
2022-04-23 sorted header location
    [211006_lmu_r0.kicad_pcb, 211006_lmu_r0.kicad_sch, file61619F33.kicad_sch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]
2022-04-24 trying out a quick thing, recover
    [211006_lmu_r0.kicad_pcb, 211006_lmu_r0.kicad_sch, Upper Address Selection.kicad_sch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]
2022-04-25 copying layout
    [211006_lmu_r0.kicad_pcb, active_passive_balance.kicad_sch, file6196A5FB.kicad_sch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]
2022-04-25 routed upper active balancer!
    [211006_lmu_r0.kicad_pcb]
2022-04-25 sorted pcb layout zones
    [211006_lmu_r0.kicad_pcb]
2022-04-25 moved micro into position
    [211006_lmu_r0.kicad_pcb, 211006_lmu_r0.kicad_sch, active_passive_balance.kicad_sch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]
2022-04-28 routed ltc3811 accessories
    [211006_lmu_r0.kicad_pcb, 211006_lmu_r0.kicad_sch, Upper Address Selection.kicad_sch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]
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2022-05-03 finished routing - beginning cleanup and review phase
    [211006_lmu_r0.kicad_sch, active_passive_balance.kicad_sch]
2022-05-07 silkscreen changes, shifting bun leds
    [211006_lmu_r0.kicad_sch, active_passive_balance.kicad_sch, file615D6D62.kicad_sch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]
2022-05-07 going to bulk edit fields
    [211006_lmu_r0-CuBottom.gbr, 211006_lmu_r0-CuIn1.gbr, 211006_lmu_r0-CuIn2.gbr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]
2022-05-07 started to export and fix things
    [211006_lmu_r0-CuBottom.gbr, 211006_lmu_r0-CuIn1.gbr, 211006_lmu_r0-CuIn2.gbr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]
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
